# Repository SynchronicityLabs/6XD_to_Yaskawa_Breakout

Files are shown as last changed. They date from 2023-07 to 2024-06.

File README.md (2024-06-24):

# 6XD_to_Yaskawa_Breakout

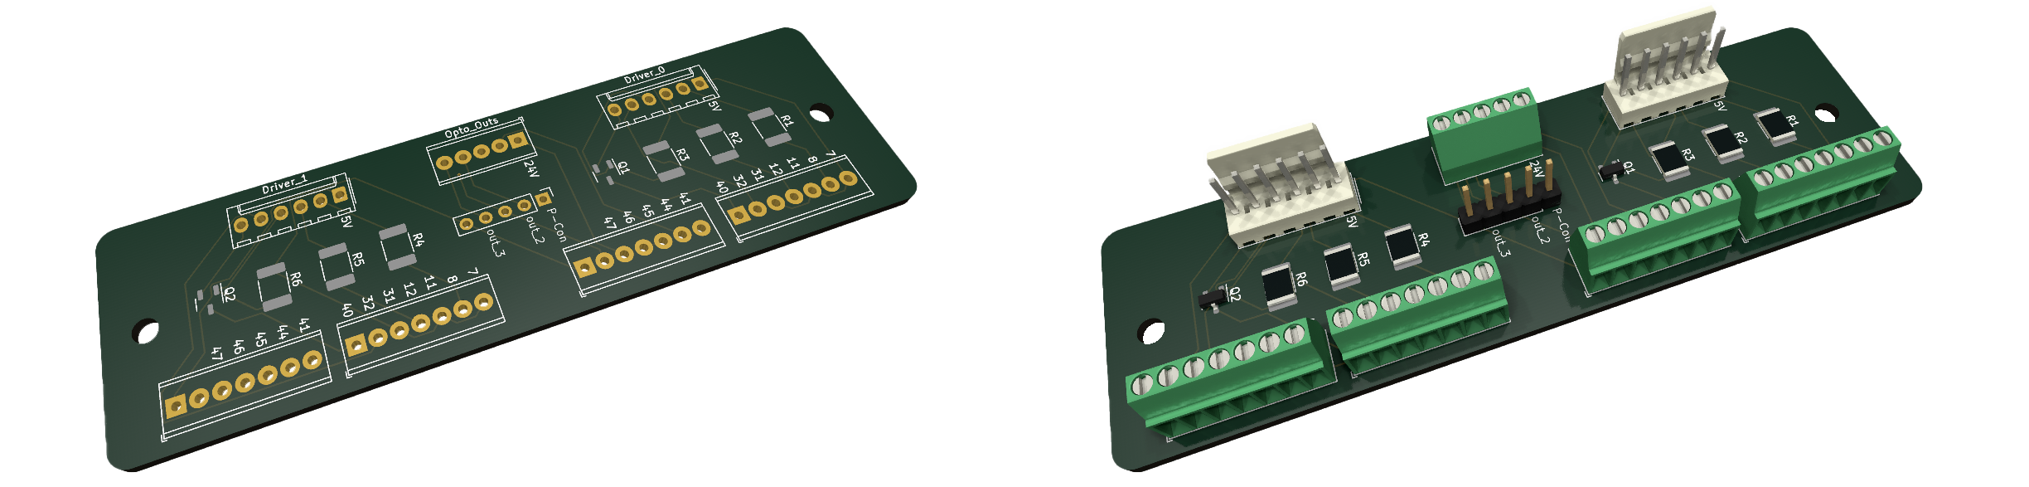
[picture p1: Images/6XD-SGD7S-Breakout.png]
Model


This is a PCB breakout board designed for connecting Yaskawa servo drives to Duet3D control boards.  Specifically, it was developed to simplify connection between a Duet 3 6XD board and a pair of Yaskawa Sigma-7 SGD7S-****00A series servo drives—i.e., step/dir-capable drives.  These drives range from 50W to 15kW, with the 50W to 400W versions (10-400W motors) being available in 100VAC or 200VAC single-phase.

This should be considered in beta! It is working on my drives, but use at your own risk!

## The board serves the following functions:
-	Correct voltage mismatch in Step/Direction signal.  The 6XD drives these signals at 5V, the SGD7S wants 3.3V
-	Allow enabling “Servo On” from the 6XD’s Dx_EN(-) pin.  The SGD7S uses a 24V enable signal which the 6XD enable pins cannot drive directly.  Set 6XD's enable jumper to "active disable".
-	Combines the torque-limit enable for forward and reverse (these are 2 separate inputs) and from both drives, to allow a single optoisolated output to trigger torque limiting for both drives, in both directions (e.g., during homing or moves prior to homing).
-	Combine the alarm reset signal for both drives to use a single optoisolated output
-	Combine the P-control enable signal for both drives to use a single optoisolated output
-	Provide a jumper to select two outputs between P-Control and two open terminal block connections (i.e., you can connect 2 of the 3)
- Block terminals and jumper allow reconfiguration of various inputs/outputs from default if desired.

### Do I need this to connect to a SGD7S servo drive?
No.  None of the connections made on the board are particularly bulky or complex; the necessary components could be joined directly into the wiring between the 6XD and SGD7S’s CN1 connector if preferred.

### Could I use this to connect a 1XD or other Duet board to a SGD7S drive?
Not recommended.  Other boards could be used, but not with the circuitry on this breakout board.  While it may seem that the 1XD would be a simple stand-in for the 6XD, it cannot directly handle the step/dir signal current for the SGD7S and would need line-driver type setup. Additionally, it cannot directly interface with the necessary inputs via IO pins (though OUT_0 and OUT_1 could), as the 6XD’s optoisolated outputs can.

### What if I want to connect more than two drives?
You could use multiple breakout boards (up to three) on a 6XD.  The opto-isolated outputs could be daisy-chained, however, you may need to ration them carefully.  The 6XD has four, with current limits of 50mA.  Each alarm-reset, P-Control, and torque-limit input takes 5mA.  So, six drives is not a problem for parallel outputs in most cases, however torque-limit signals from a single output would be maxed out at 5 drives. 

### Where do I find you if I blow up my drives/Duet?
You don’t, this is currently beta-version at best.  The SGD7S manual is nearly 650 pages.  I’ve tried to make it simple here, but it isn’t.  Your drive connections are at your own risk.

### Can it interface to drives other than the SGD7S drives?
Probably.  Good luck, we all believe in you.

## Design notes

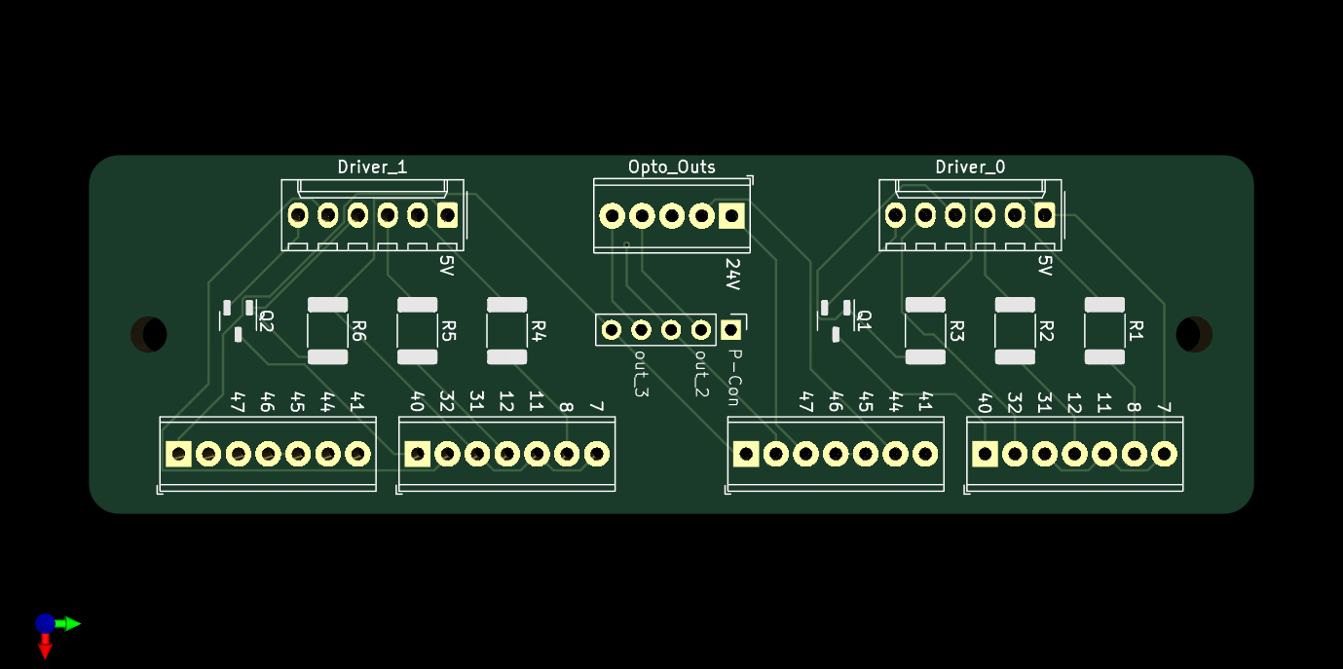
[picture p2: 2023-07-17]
Images/6XD-SGD7S board-front.png

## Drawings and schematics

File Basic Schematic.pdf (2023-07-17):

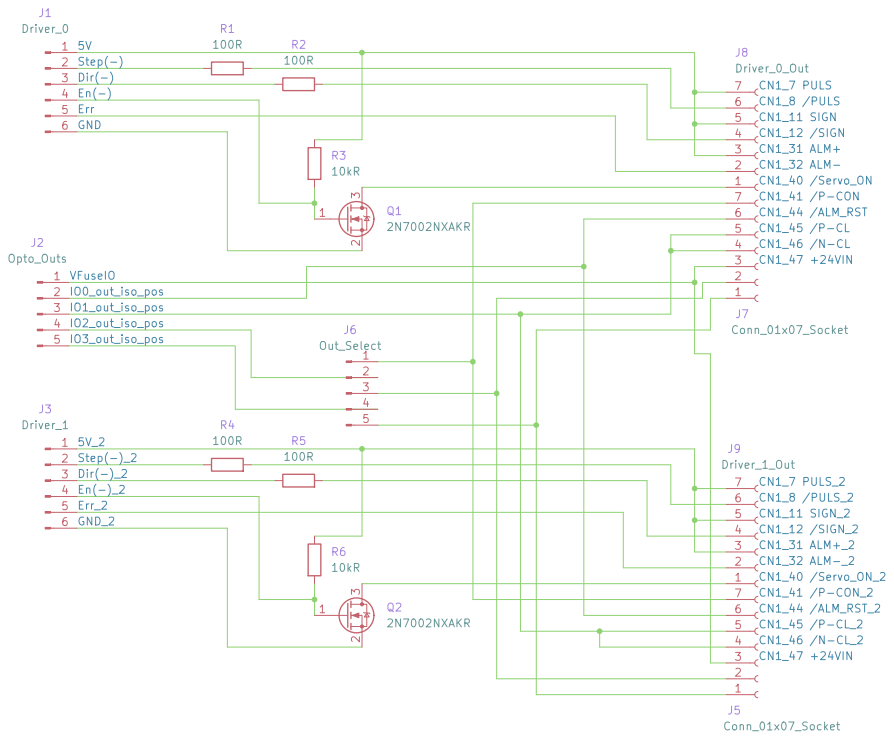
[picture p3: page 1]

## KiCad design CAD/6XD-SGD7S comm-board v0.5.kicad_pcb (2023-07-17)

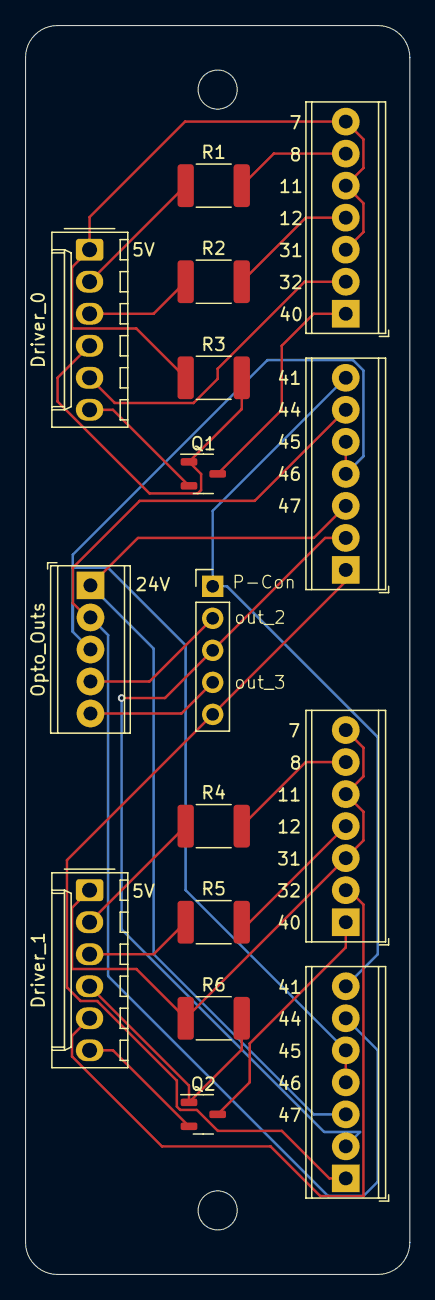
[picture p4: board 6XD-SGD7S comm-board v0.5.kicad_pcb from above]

Board: 2 copper layers, 30.5 x 99.1 mm, 16 parts (0 on the bottom side), 26 nets.

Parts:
J1: Driver_0; Molex_KK-254_AE-6410-06A_1x06_P2.54mm_Vertical
J2: Opto_Outs; TerminalBlock_Phoenix_MPT-0,5-5-2.54_1x05_P2.54mm_Horizontal
J3: Driver_1; Molex_KK-254_AE-6410-06A_1x06_P2.54mm_Vertical
J5, J7: Conn_01x07_Socket; TerminalBlock_Phoenix_MPT-0,5-7-2.54_1x07_P2.54mm_Horizontal
J6: Out_Select; PinHeader_1x05_P2.54mm_Vertical
J8: Driver_0_Out; TerminalBlock_Phoenix_MPT-0,5-7-2.54_1x07_P2.54mm_Horizontal
J9: Driver_1_Out; TerminalBlock_Phoenix_MPT-0,5-7-2.54_1x07_P2.54mm_Horizontal
Q1, Q2: 2N7002NXAKR; SOT-23-3
R1, R2, R4, R5: 100R; R_1812_4532Metric_Pad1.30x3.40mm_HandSolder
R3, R6: 10kR; R_1812_4532Metric_Pad1.30x3.40mm_HandSolder

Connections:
/5V: J1.1, J8.3, J8.5, J8.7, R3.1
/5V_2: J3.1, J9.3, J9.5, J9.7, R6.1
/Dir(-): J1.3, R2.1
/Dir(-)_2: J3.3, R5.1
/En(-): J1.4, Q1.1 (G), R3.2
/En(-)_2: J3.4, Q2.1 (G), R6.2
/Err: J1.5, J8.2
/Err_2: J3.5, J9.2
/GND: J1.6, Q1.2 (S)
/GND_2: J3.6, Q2.2 (S)
/IO0_out_iso_pos: J2.2, J5.6, J7.6
/IO1_out_iso_pos: J2.3, J5.4, J5.5, J7.4, J7.5
/IO2_out_iso_pos: J2.4, J6.2
/IO3_out_iso_pos: J2.5, J6.4
/Step(-): J1.2, R1.1
/Step(-)_2: J3.2, R4.1
/VFuseIO: J2.1, J5.3, J7.3
unnamed: J5.1, J6.5, J7.1
unnamed: J5.2, J6.3, J7.2
unnamed: J5.7, J6.1, J7.7
unnamed: J8.1, Q1.3 (D)
unnamed: J8.4, R2.2
unnamed: J8.6, R1.2
unnamed: J9.1, Q2.3 (D)
unnamed: J9.4, R5.2
unnamed: J9.6, R4.2

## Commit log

2023-07-17 Update and rename 1XD-SGD7S comm-board.kicad_sch to 1XD-SGD7S comm-board v0.5.kicad_sch
    [1XD-SGD7S comm-board v0.5.kicad_sch]
2023-07-17 Update and rename 6XD-SGD7S comm-board.kicad_pcb to 6XD-SGD7S comm-board v0.5.kicad_pcb
    [6XD-SGD7S comm-board v0.5.kicad_pcb]
